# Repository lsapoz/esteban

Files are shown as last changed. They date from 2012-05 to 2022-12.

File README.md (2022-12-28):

# Northwestern Design Competition 2012

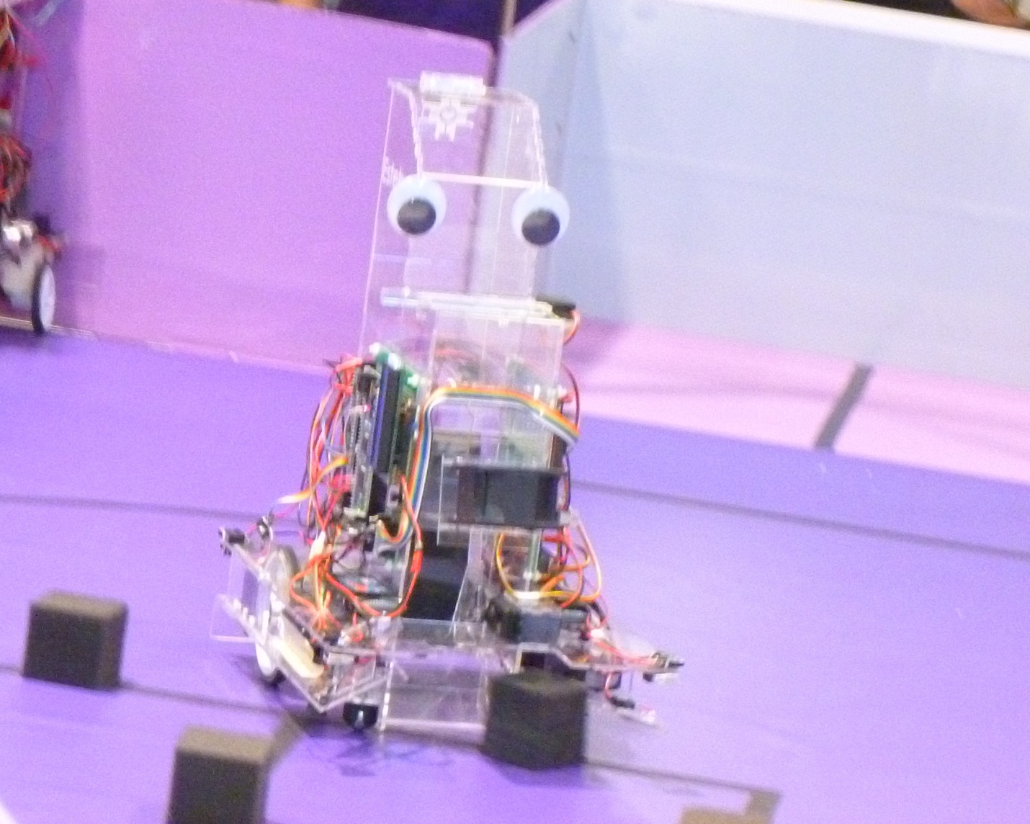
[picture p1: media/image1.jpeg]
Esteban


## Overview

I was cleaning up my dropbox and stumbled upon all the files for Esteban, the robot Michael Chen and I built for the 2012 Northwestern Autonomous Robot Design Competetion. I thought github would be a better place to host the files, so here we are.

Since all the code was stored as snapshots (i.e. the [Final.doc](https://phdcomics.com/comics.php?f=1531) approach to version control), I turned each snapshot into a distinct commit and spoofed the dates using [git-redate](https://github.com/PotatoLabs/git-redate). 

## Related Links
- [El Viaje de Esteban](https://viajedeesteban.tumblr.com/) - a project blog chronicling the build
- [Match Video](https://www.youtube.com/watch?v=B897-lxEE_c)
- [Competition Rules](https://sites.google.com/site/dcnuinfo/previous-competition-rules/2012-competition-rules)
- [Mechatronics Lab Wiki](http://hades.mech.northwestern.edu/index.php/Northwestern_Design_Competition#DC2012)
- [Article](https://www.mccormick.northwestern.edu/news/articles/2012/05/2012-design-competition-winners.html)

## The Team

The team consisted of myself, a mechanical engineering junior, and
Michael Chen, a civil engineering junior. This was our second design
competition.

All aspects of the design were done together. This covers the initial
brainstorming of ideas, building mockups to see what worked and what
didn't, and all major mechanical, electrical, and software design
decisions. For example, deciding the dimensions of a part, discussing
what kind of circuit would accomplish a task best, and what sort of
approach an algorithm would take to tackle a problem were all at the
very least discussed. As a result, both of us have an intimate knowledge
of every aspect of the robot.

In actually building the robot, tasks were often split up to maximize
efficiency. However, we would often work on parts in tandem so that we
could still talk to each other about what we were doing. So while we
designed the chassis together, I was the one who actually created all of
the CAD files and used them to cut out the chassis on the laser cutter.
I also wrote all of the code that the robot ran on. However, Mike would
go in and tune different parts of the code that needed tuning. Mike also
implemented most of the electrical design.

The product of our work was the robot named Esteban. He bore two giant
googly eyes which served as the namesake for our team: "Googly Eyes."

## Strategy

A quick run-down of the competition revealed three key points that would
end up influencing our design above all others

-   The cubes were made out of a light foam which could not be detected
    easily from afar with simple sensors

-   Three times as many points were scored for cubes deposited in the
    bonus zone rather than the regular scoring zone

-   There are massive penalties for manipulating more than five cubes at
    a time

Early on we resigned ourselves to trying to find cubes using some sort
of efficient random algorithm rather than actually detect them. This was
based on the assumption that cubes would be moved around a lot during
the competition. Later on we realized that actually programming in
several possible hard coded paths was a more reliable option. We would
program paths meant to drive over the starting positions of 8 or so
cubes. However, after four cubes were actually picked up we would exit
the path and drive towards the scoring zone to deposit them.

Encoders were used for keeping track of Esteban's location. Because of
collisions and the moving scoring zone, we needed to reset our location
often. Resetting on the long axis was accomplished by driving over the
center line. Resetting after exiting the scoring zone was done by
hitting one of the side walls to reset angle, and then using either the
center line or a cube to reset overall position.

We couldn't detect cubes from afar, but a series of break beams were
used to determine when they entered our chassis. We took advantage of
the cube's light material by using two fans: one to blow them into a
tower and one to blow them out.

A laser attached to a servo was used to find the scoring zone, which was
covered in retroreflective tape. Esteban turns himself so that his back
is facing the scoring zone and then drives towards the center line, 6
feet away from the zone. The laser is then swept, and the "average"
angle of the laser for which the beam bounces back is found. Esteban
then turns this average angle and begins to drive towards the zone. The
same technique is repeated three feet from the zone and one and a half
feet from the zone. This helps adjust for the movement of the zone.

## Mechanical Design

### Parts list

-   3 acrylic sheets -- 0.118"x12"x24"

-   1 1.5" acrylic hinge

-   1 4" long 3/8" diameter acrylic rod

-   2 90mm wheels

-   2 4mm universal mounting hubs

-   2 ¾" metal ball casters

-   2 drive motors

-   2 small servos

-   1 large servo

-   1 laser

-   7 bright red LEDs

-   8 phototransistors

-   8 push buttons

-   2 capacitive encoders

-   1 60mm case fan

-   1 80mm case fan

-   4 7.4 V polymer lithium ion batteries

-   1 11.1 V polymer lithium ion battery

-   A pair of 40mm googly eyes

### Chassis CAD Drawing

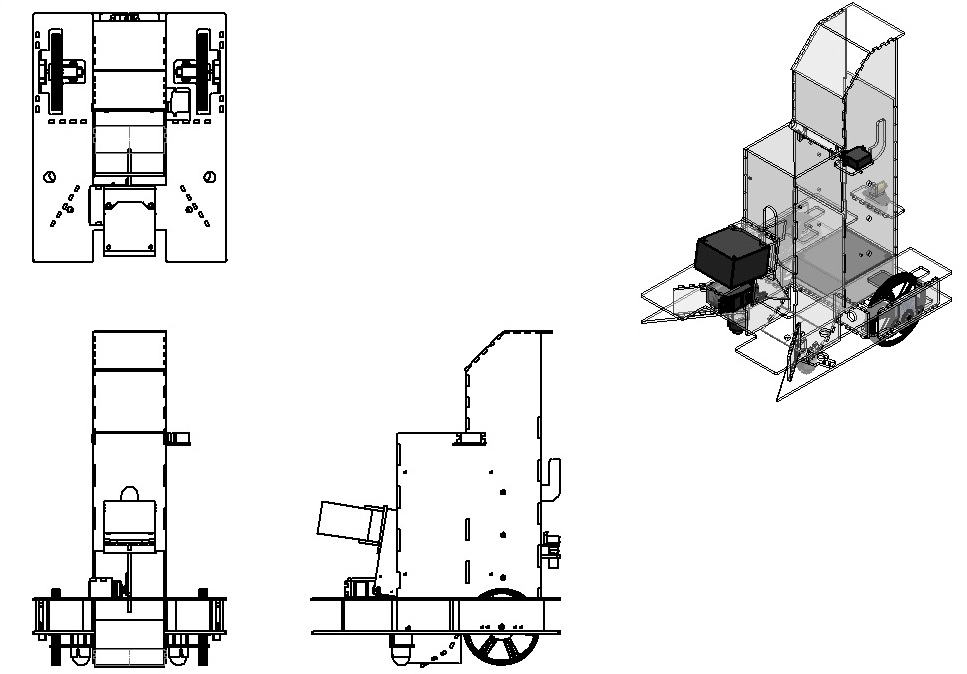
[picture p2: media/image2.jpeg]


### CAD -- Sheets for Laser Cutting

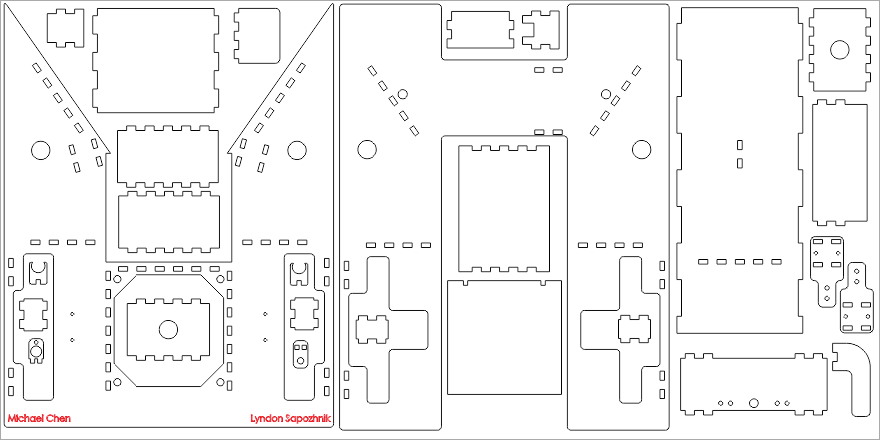
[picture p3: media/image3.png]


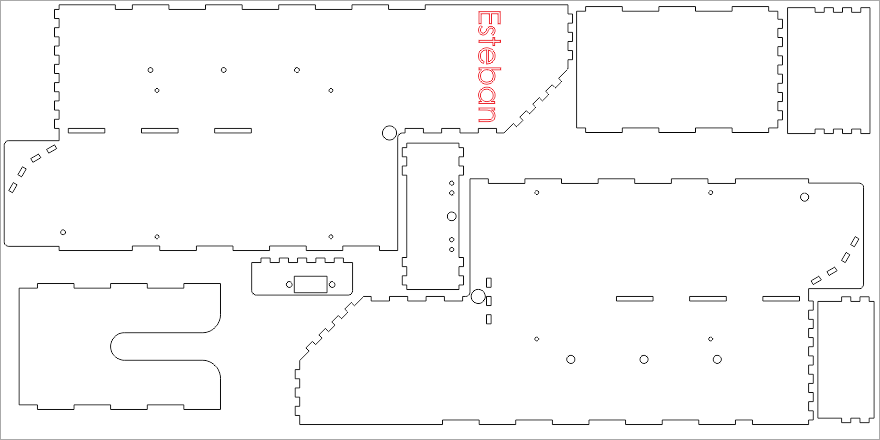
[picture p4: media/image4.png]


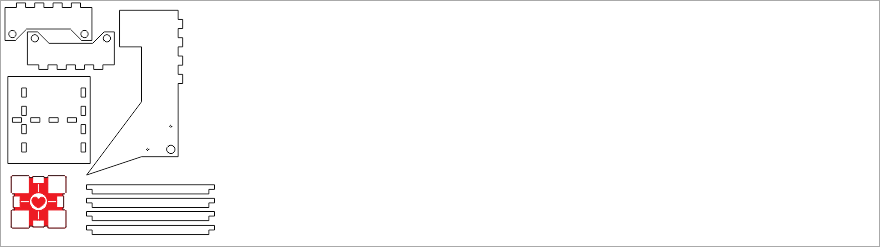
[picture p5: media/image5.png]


### Locomotion Technique

The two drive motors provided to us were used to move Esteban. They were
placed towards the back. Two metal ball casters were placed near the
front for balance.

PID motion control based on encoder feedback was implemented to control
the motors. The hope was that this would allow us to set a speed that
both motors would adhere to with little error, allowing for Esteban to
drive in straight lines and turn accurately. Unfortunately, a number of
things prevented this from working well in practice. One was that the
wheels would actually lift off the ground while driving. This was fixed
by placing steel bars by the wheels to weight them down and keep them on
the ground. Another was the poor relationship between voltage and speed;
setting a constant voltage would result in a widely varied speed. This
meant that even when controlling for the voltage using motion control,
the resulting speed would still vary so much that Esteban ended up
veering left or right while driving.

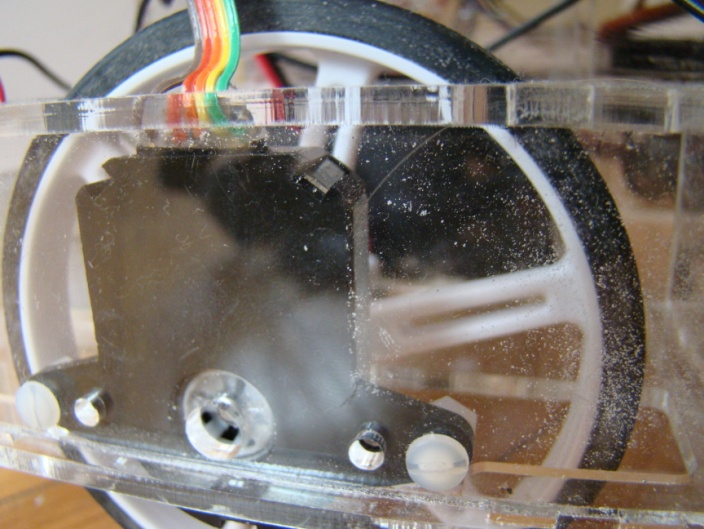
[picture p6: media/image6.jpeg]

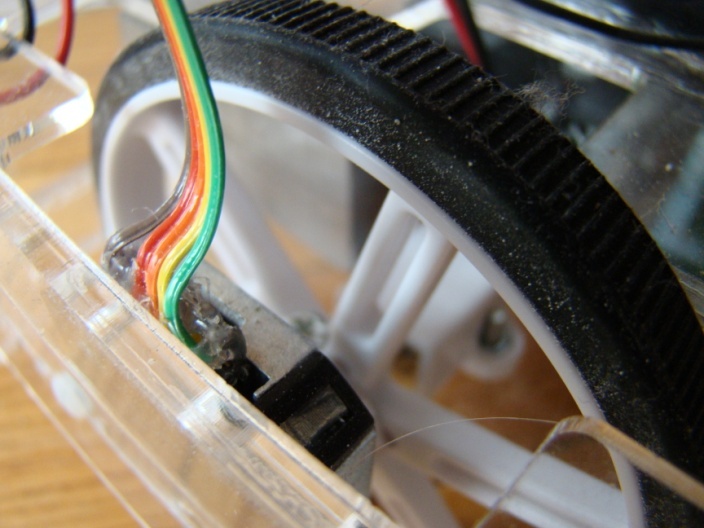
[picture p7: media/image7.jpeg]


Eight push buttons were used for collision detection; two at each
corner. The two at each corner are tied together so we only had
information about which corner was colliding with something.

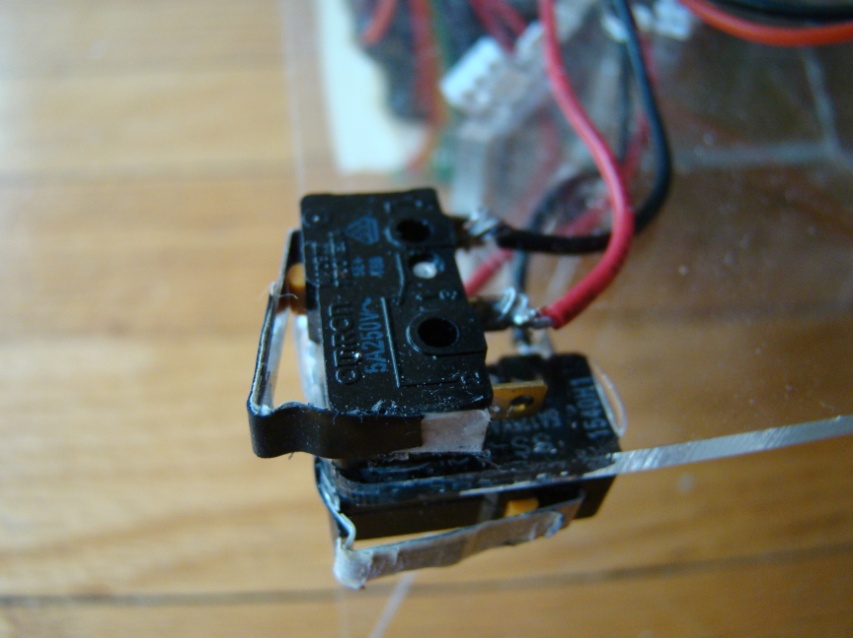
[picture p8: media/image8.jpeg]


### Interaction with the cube

The front of Esteban is shaped like the letter "V," wide at the front
and narrowing down to a channel slightly wider than the cubes. Once a
crate is detected, a 60mm case fan is lowered using an acrylic arm and
turned on. This blows the cube up onto a ramp and into Esteban's tower.

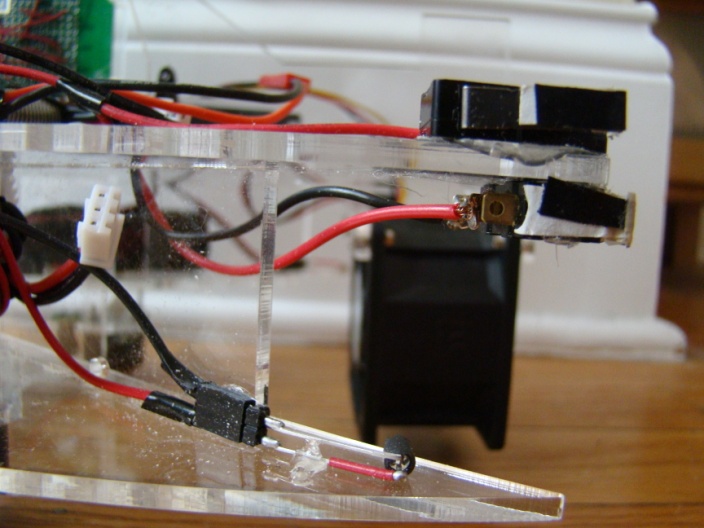
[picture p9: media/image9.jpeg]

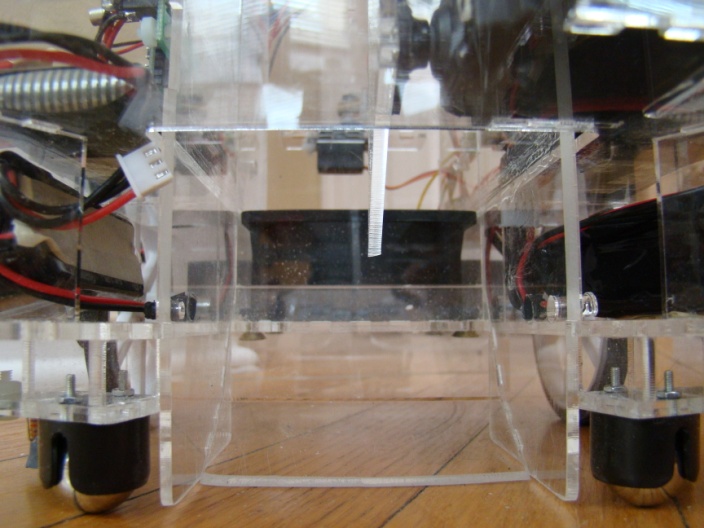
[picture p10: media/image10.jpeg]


Entrance into the tower was controlled by a door attached to a servo.
The door was opened to let cubes in and closed to keep them in. Once
Esteban was in the scoring zone, he would drive to the back wall and
turn on the tower fan, which would blow all the cubes out.

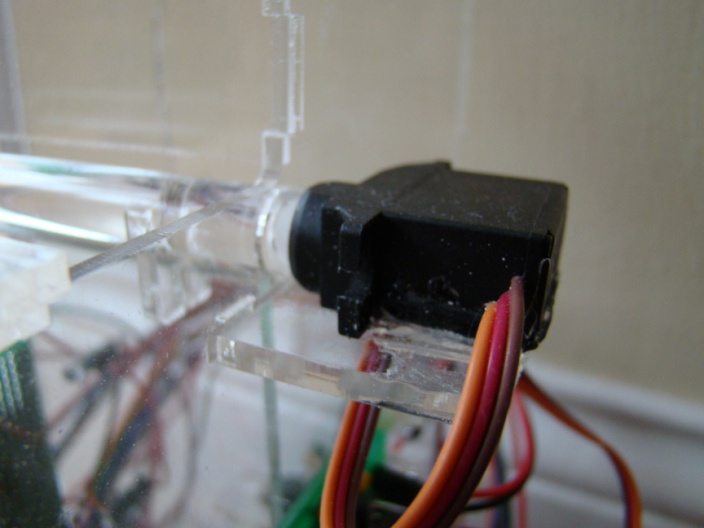
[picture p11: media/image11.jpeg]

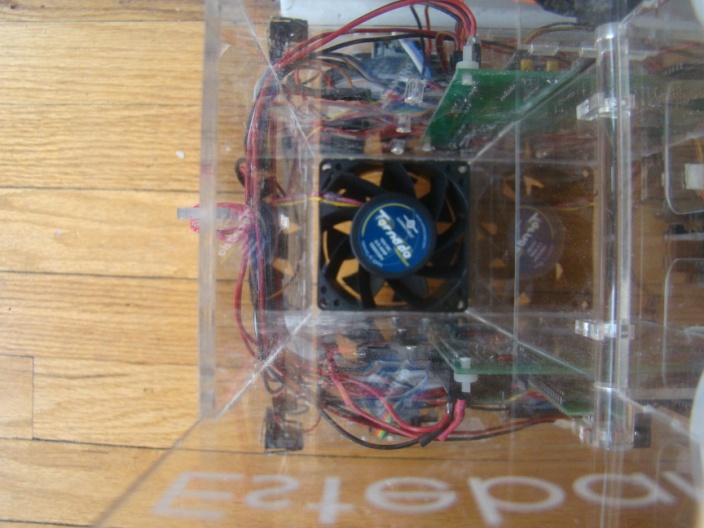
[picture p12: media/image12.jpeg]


To keep the cubes from shooting out too far and missing the bonus zone,
a "doggy door" was attached to the exit using an acrylic hinge. This
alters the cubes trajectory so they point downwards more than straight
out.

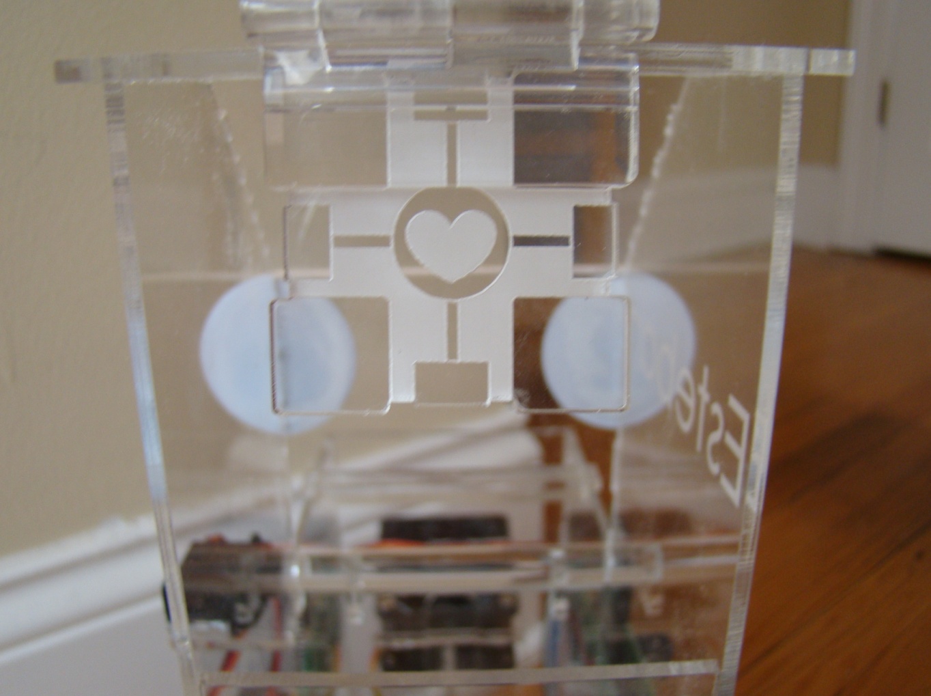
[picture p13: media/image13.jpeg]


The tower was capable of holding up to three cubes. The fourth cube was
stored just outside the tower. The front fan would be turned on but the
tower door would be kept closed, causing the cube to be shot up until it
hit a thin acrylic barrier. The front fan would then be turned off and
rotated back into its resting position. Thanks to the fan arm's unique
shape, it actually holds the fourth cube in place. We can then blow it
into the tower at a later point.

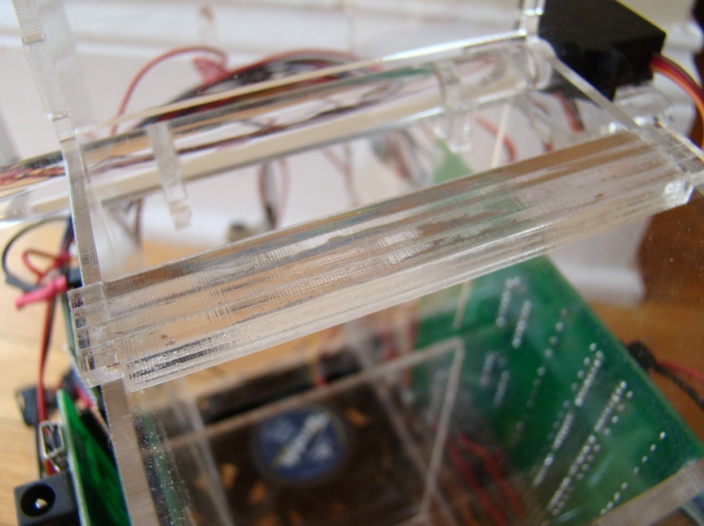
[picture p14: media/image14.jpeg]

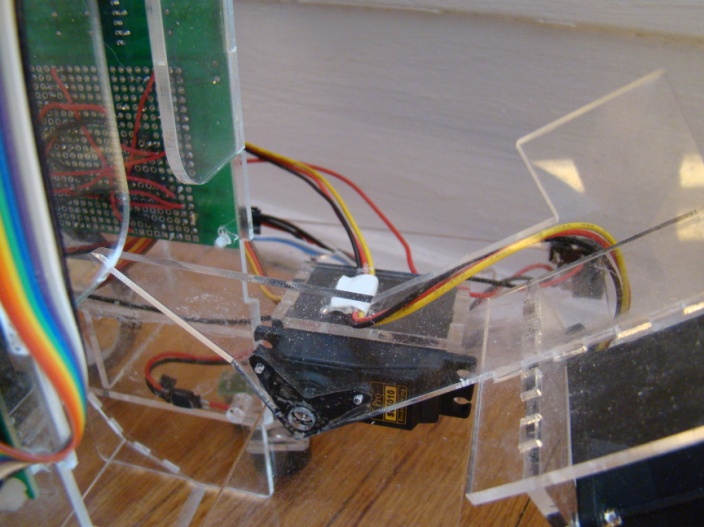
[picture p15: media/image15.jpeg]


## Electrical Design

### Actuator Controllers

One large servo was used to control the fan arm. One small servo was
used to control the tower door, and another was used to control the
laser.

### Sensors

Five breakbeam sensors were used for detecting cubes inside Esteban: one
at the very front of the chassis, one just in front of the channel (near
the middle of the chassis), and three in the tower. The breakbeam
sensors were simply a bright LED pointing at a phototransistor. To
control for ambient light, we would read the phototransistor twice in a
cycle: once with the LED on and once with it off. We would use the
difference between the two readings as our check; if it dipped to 0, we
knew a cube was there.

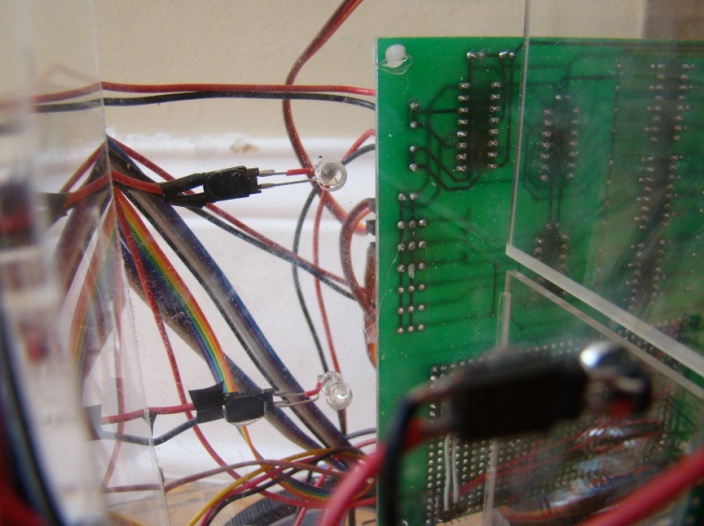
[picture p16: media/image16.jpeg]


Two color sensors were used for determining the current color of the
board. They were simply an LED and phototransistor placed next to each
other, pointed at the ground. White reflected a lot, purple
significantly less, and black almost not at all. The two color sensors
were "pulsed" just as the breakbeams were to control for ambient light.
Heat shrink was used as an additional precaution.

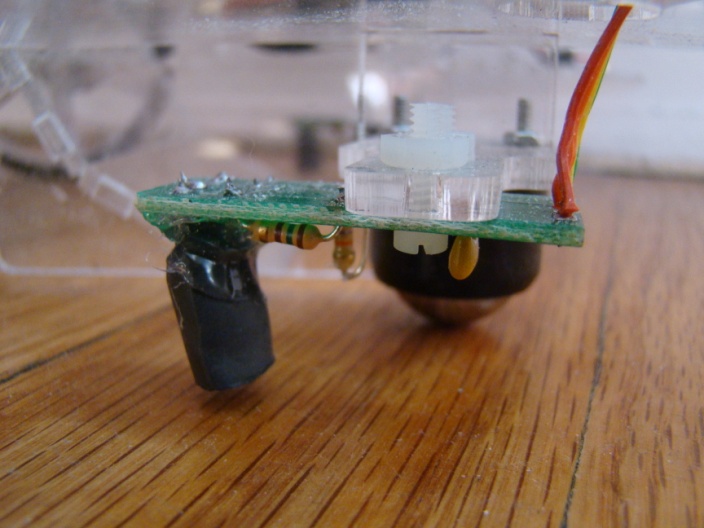
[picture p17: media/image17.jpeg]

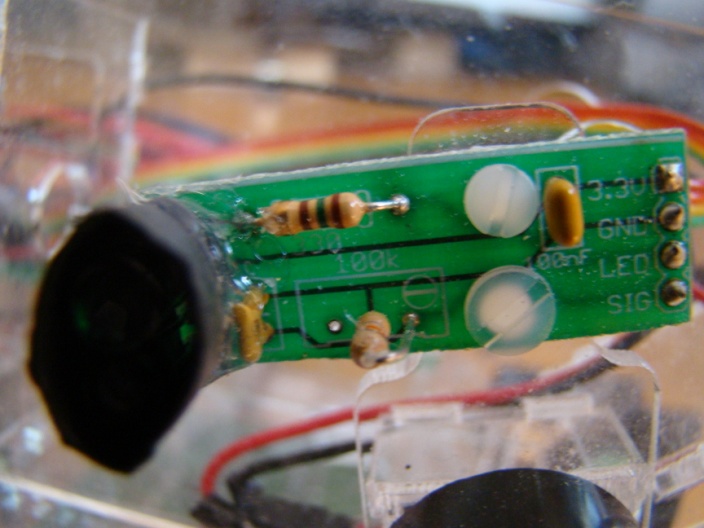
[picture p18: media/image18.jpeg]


A laser/phototransistor combo attached to a servo was used for finding
the scoring zone. It was blinked on and off in the same way the LEDs
were to control for ambient light.

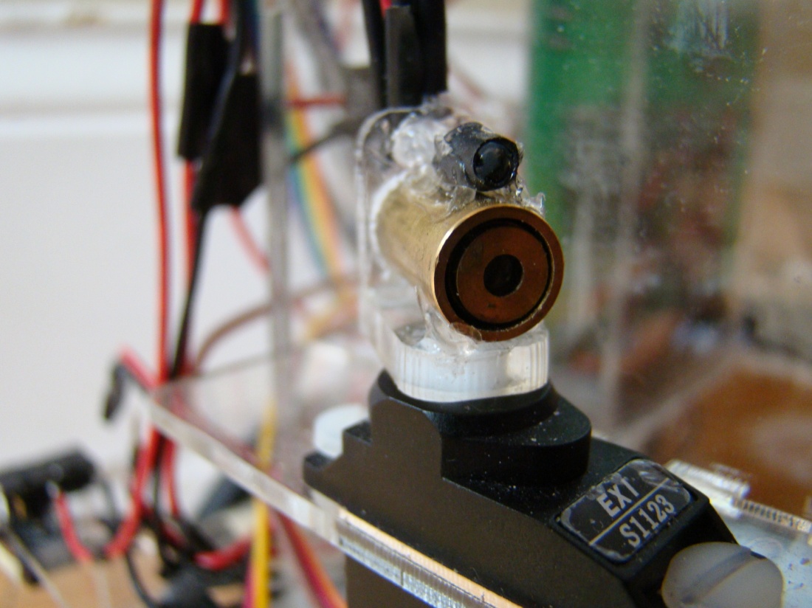
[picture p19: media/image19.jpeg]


The encoders used for motion control and location awareness were each
fed into their own dsPIC33. These were then connected to the main PIC32
using SPI communication.

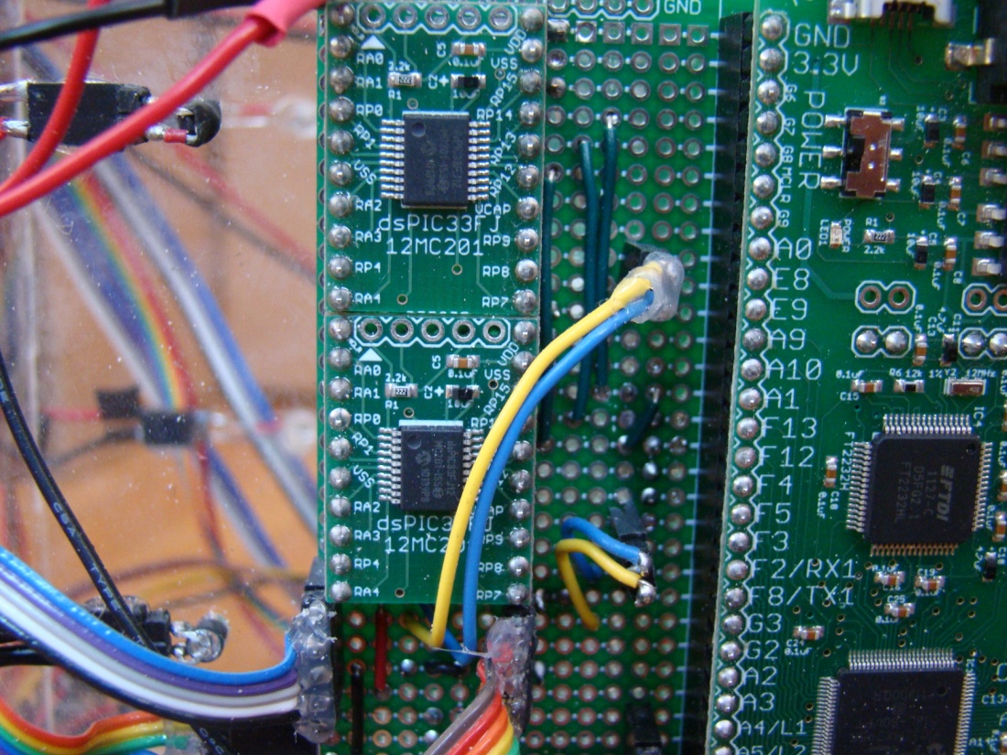
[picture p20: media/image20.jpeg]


All the sensors were connected to the PIC32 in the following way:

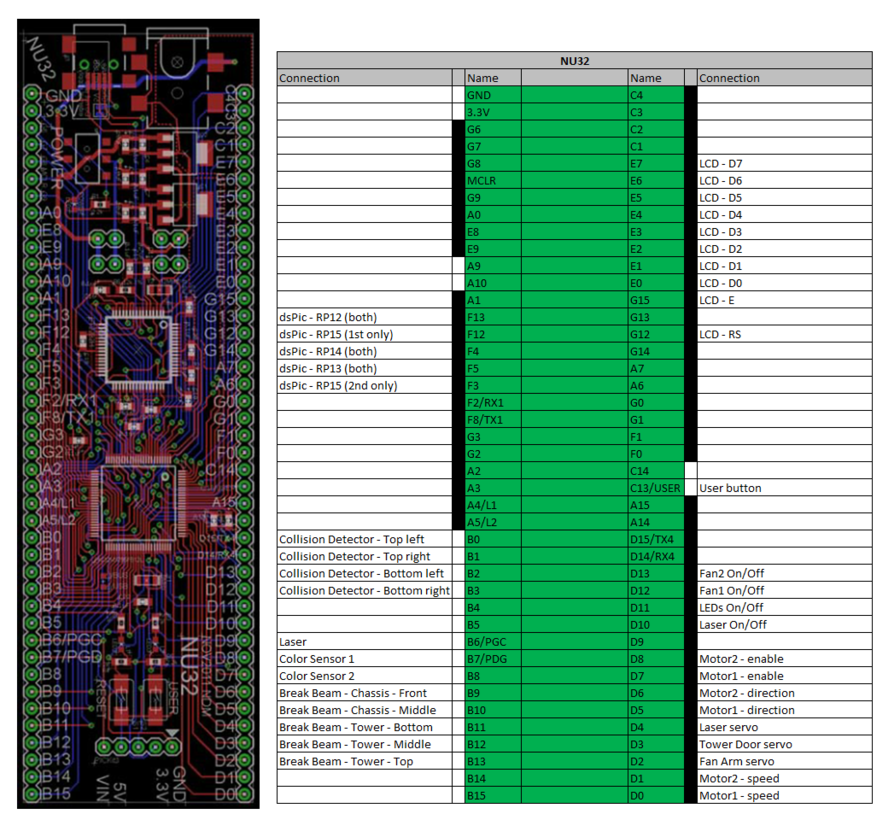
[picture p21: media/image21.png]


### Power Management

Rechargeable polymer-lithium ion batteries were used this year. All were
connected to voltage regulators so that the same voltage would be always
supplied to our components. One 7.4 V battery was used to power the
PIC32, one to power the logic, and two in series to power the fans. One
11.1V battery was used to power the motors.

### Breakout Boards

The two breakout boards were mounted to Esteban's sides.

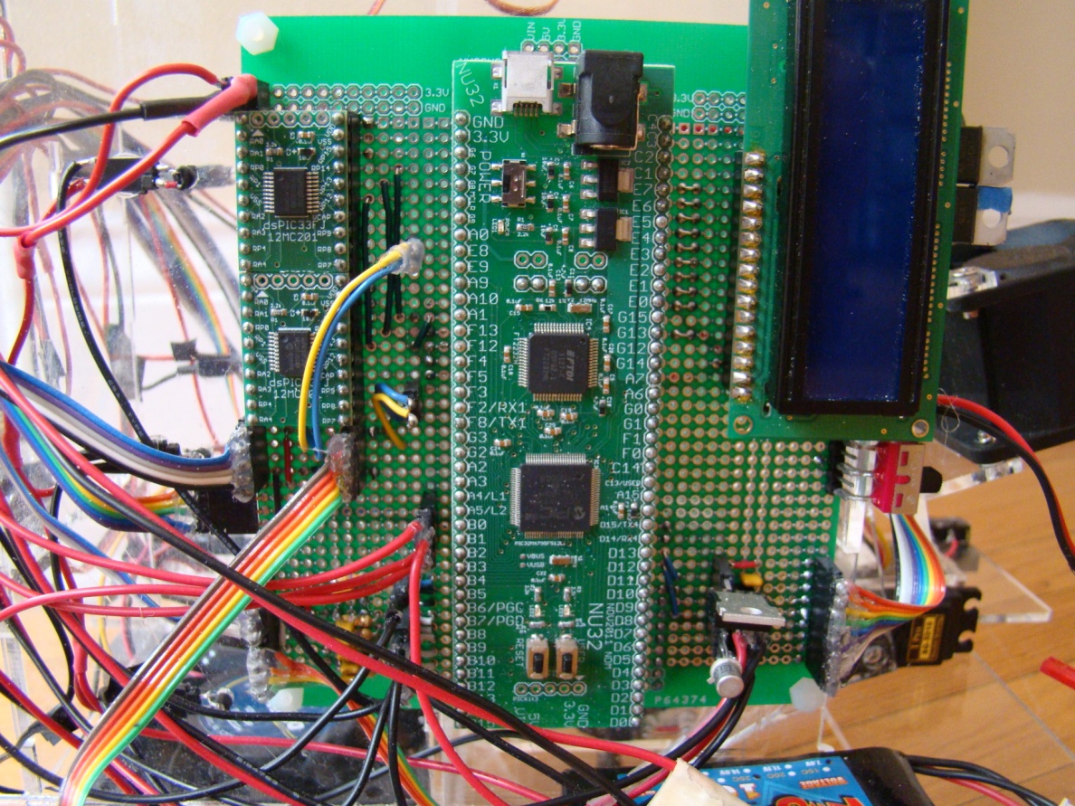
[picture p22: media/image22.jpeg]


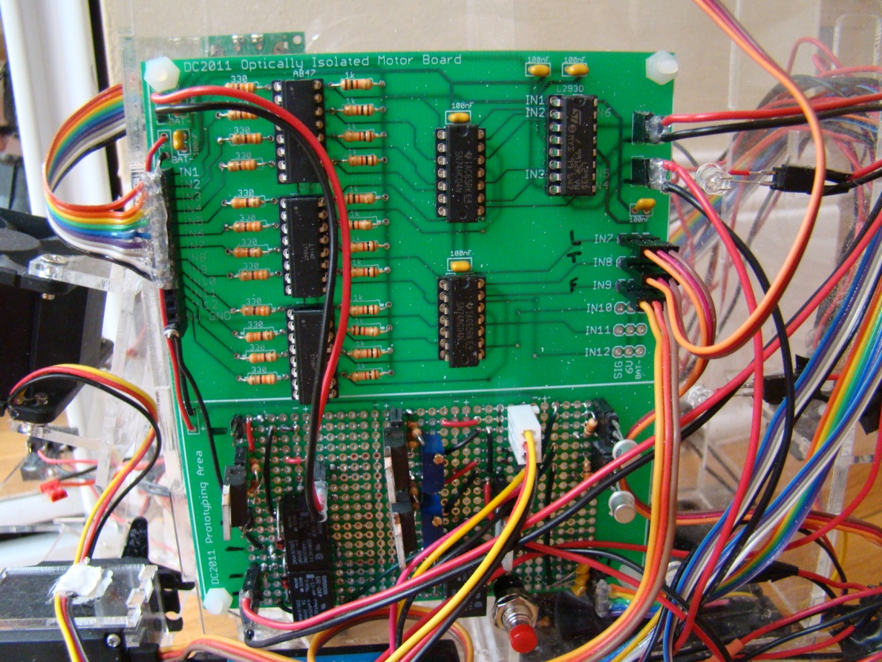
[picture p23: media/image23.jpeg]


## Programming

The program was split across four user written files + four provided
(NU32.h and .c, LCD.h and .c).

They were:
```c
- main.h     // initialization and interrupts
- data.h     // definition of constants, conversion formulas, and global variables
- library.h  // declaration of all functions
- library.c  // initialization of all functions
```

### Functions
```c
// Timer functions

void initCoreTimer(void); // initialize the core timer to interrupt every 1 ms

void initTimer4Interrupt(void); // turn on timer4 interrupt at 250 Hz

void initTimer5Interrupt(void); // turn on timer5 interrupt at 10 Hz

// Pin Initialization functions

void initChangeNotification(void); // enable pull up resistors for collision detection pins

void initDigitalOut(void); // enable all digital outs

void initAnalogInput(void); // read in all used analog in pins

void initOutputCompare(void); // turn on both motors and all three servos

// Encoder functions

void initEncoderSPI(void); // initialize SPI communication with the dsPICs at 8MHz

long getEncoder1(int reset); // get the current number of ticks of encoder1

long getEncoder2(int reset); // get the current number of ticks of encoder2

// Servo functions

void rotateFanArm(int servoPos); // rotate the fan arm to a desired position

void rotateTowerDoor(int servoPos); // rotate the tower door to a desired position

int sweepLaser(float feet); // sweep the laser and calculate the distance to the zone

// Fan functions

void blowCubeIn(); // blow a cube into the tower

void blowCubeUp(); // blow a fourth cube up outside of the tower for storage

void blowCubesOut(); // blow all cubes in the tower out

void blowCubeInAndOut(); // blow the fourth stored cube into the tower and straight out

void checkForCubes(); // while driving, stop if a cube is detected so it can be captured

// Driving Functions

void setMotorSpeed(int dutyCycle1, int dutyCycle2); // set the voltage for both motors

void reverseDirection(); // change the voltage appropriate to drive in reverse

void driveDistance(float inches, int mode); // drive forwards or backwards a certain distance

void turnAngle(int degrees); // turn a certain amount of degrees

void driveToCenter(); // drive until the center line (i.e. ground color changes)

void driveToZone(); // drive to center, sweep laser multiple times on the way to the scoring zone

void resetAngle(); // keep colliding and adjusting angle until perpendicular

void resetAngleOnWall(int wall); // collide with the wall until perpendicular

void resetAngleInZone(); // collide with the back wall until perpendicular

void exitAndResetOnRight(); // exit the scoring zone and reset angle on the right wall

void exitAndResetOnLeft(); // exit the scoring zone and reset angle on the left wall

// Sweep Patterns

void firstSweepPattern1(); // first cube in front, two on middle line, one on first line

void firstSweepPattern2(); // first cube in front, three on second line

void firstSweepPattern3(); // the four cubes on the diagonal from the starting position

void firstSweepPattern4(); // reset angle on wall at center line, then all on middle line

void firstSweepPattern5(); // the four closest cubes

void secondSweepPattern1(); // three on middle line, two on fourth line

void secondSweepPattern2(); // first cube upon resetting on right wall

void secondSweepPattern3(); // three on diagonal leading from the cube in secondSweepPattern2();

void randomSweepPattern(); // drive completely randomly

void wallToWallSweepPattern(); // sweep the entire field, wall to wall

// Stringing it all together

void firstSweep(); // firstSweepPattern4()+exitAndResetOnRight()

void secondSweep(); //secondSweepPattern2()+3()+ exitAndResetOnLeft()

void randomSweep(); // drive randomly searching for cubes
```
### main

#### main
```
{
    Call every initialization function
    while (1) {
        if (user button is pressed) {
            firstSweep();
            secondSweep();
        }
    }
}
```

#### Core Timer Interrupt (1000 Hz)
```
{
    increment the global time variable
}
```

#### Motion Control Interrupt (250 Hz)
```
{
    Read in encoder1 and encoder2 and perform PID control based on the driving state (driving straight or turning)
}
```

#### Sensor Interrupt (10 Hz)
```
{
    Turn on all the LEDs
    Read all the phototransistors
    Turn off all the LEDs
    Read all the phototransistors
    Calculate the difference between the ON and OFF values
    Determine the number of crates in the machine
    Determine the color being read by the color sensors
    Determine if any collision detectors are being tripped
}
```

## Results

### Midterm Milestone

For the midterm milestone, we had cut and assembled the first version of
Esteban. While testing with him we found that cubes would often get
stuck inside Esteban because they very easily rotate; we had to design
for 2 √3, not 2 √2. In order to make sure the cubes could traverse
Esteban's interior once we expanded relevant dimensions, we rather
recklessly tore him apart and taped him back together. Once we were
satisfied we began altering the design. In the meantime, "Frankenbot"
was used to clear the Midterm Milestone.

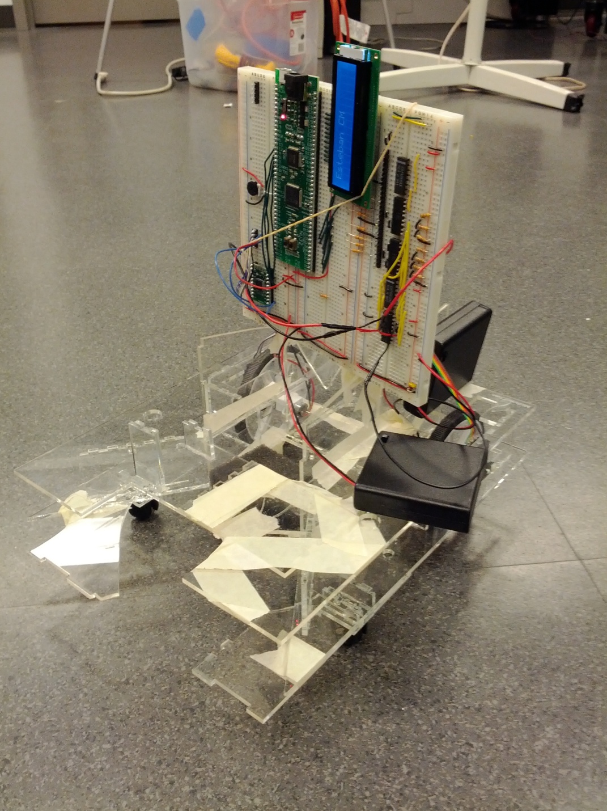
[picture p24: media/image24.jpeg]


### Pre-Competition Demonstration

Every single system but driving was up and running great for the
pre-competition demonstration. We still had issues getting the robot to
drive in a straight line reliably, but Esteban was at least turning
fairly accurately. What remained for the final week was fixing this
issue to the best of our ability, and actually coding in strategy.

### Competition Results

Getting the robot to drive straight accurately was an exercise in
frustration. We began to throw in a whole host of precisely tuned
constants into the PID motion control code, making something that was
once simple into something horrendously complex. Additionally, these
constants had to be retuned as our motors degraded. In the 24 hours
leading up to the competition, both of our motors ended up losing the
ability to drive backwards and had to be replaced. After these accidents
we decided to only tune what we thought were our two best paths for the
competition. We decided that consistency would probably pay off in the
competition more than diversity.

The decision ended up paying off, as we were seeded first and we won
first place. Esteban successfully executed his two paths each time.
Occasionally we would drift too left or right to pick up a cube we had
intended to pick up. One time a cube overshot the bonus zone and fell
out of the arena. But we always ended our rounds with at least six cubes
in the bonus zone. That was enough to carry us to victory.

## Takeaways

Thanks to the lessons learned from competing in last year's design
competition, we understood what needed to be done this year to build a
great robot. Esteban was very precisely engineered, and it shows. He
executed everything we meant for him to do exactly as we meant for him
to do it, with the exception for driving.

We meant to use some sort of feedback control for driving this year, and
our choice of PID simply did not cut it. Perhaps we would have gotten
better performance had we based the motion control on current control
rather than just encoder feedback. If there had been time, I would have
definitely explored more avenues of getting reliable driving.

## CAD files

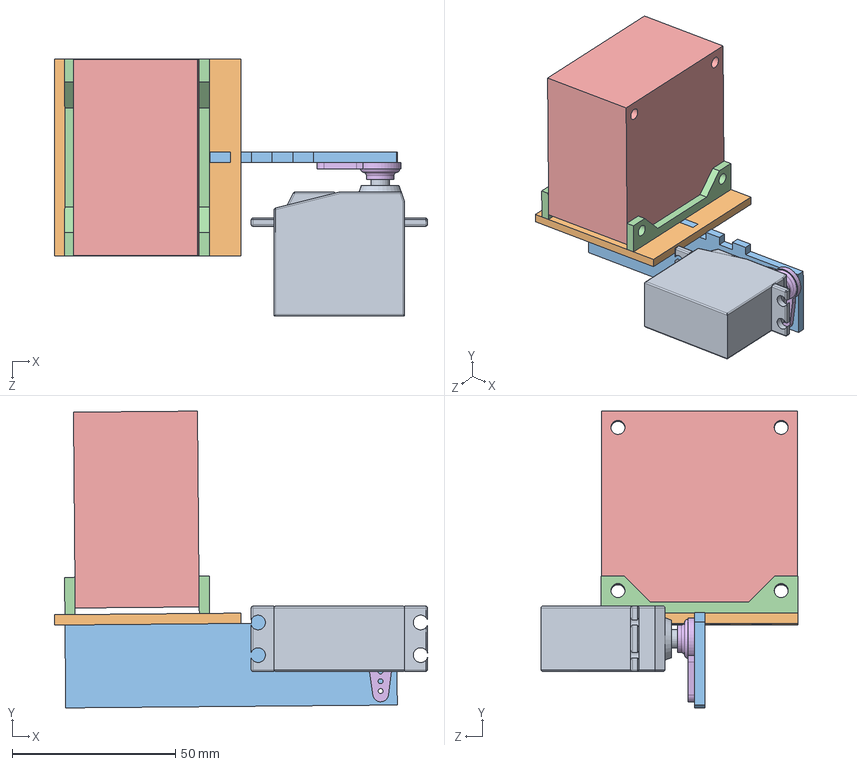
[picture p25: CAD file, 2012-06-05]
model/fan_arm.SLDASM
114.3 x 90.9 x 78.8 mm
servo_large
fan_arm_horizontal
fan_arm_vertical
fan_arm_holder x 2
fan_60mm
servo_handle_two

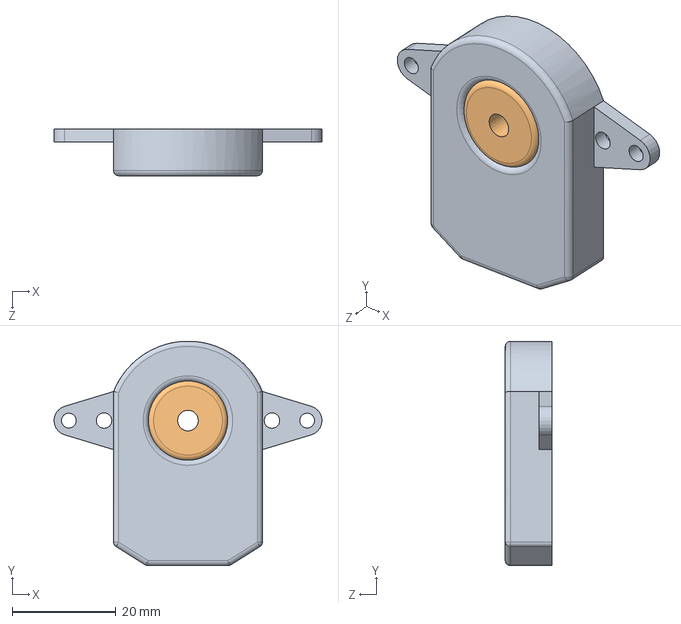
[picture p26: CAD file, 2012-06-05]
model/encoder.SLDASM
51.8 x 43.4 x 9.00 mm
encoder_base
encoder_sleeve

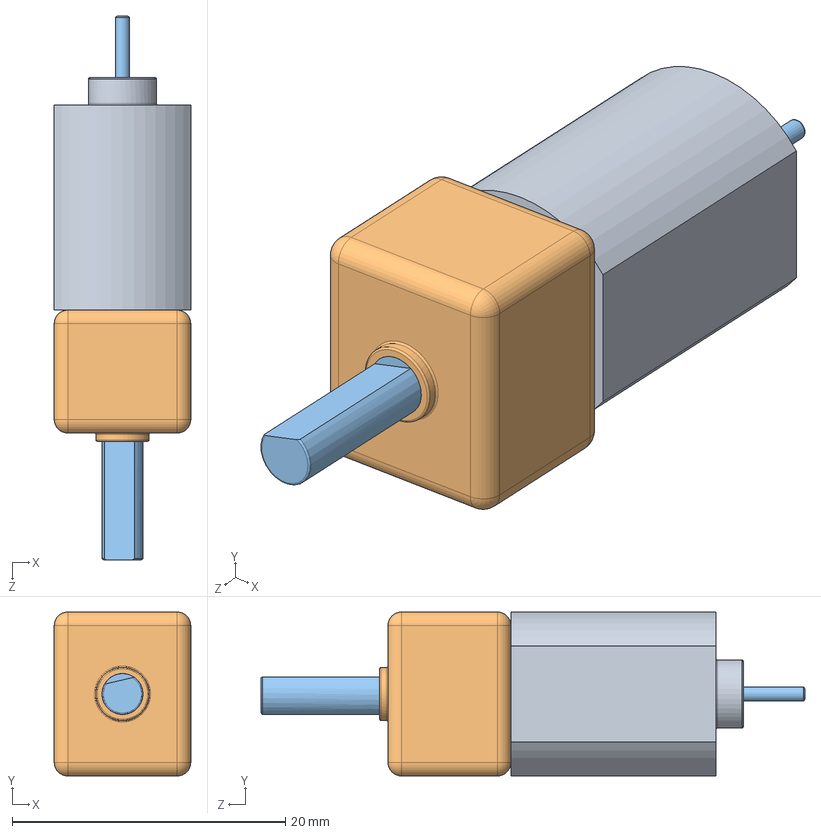
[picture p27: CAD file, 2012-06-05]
model/motor.SLDASM
10.0 x 12.0 x 39.8 mm
motor_casing
motor_gearbox
motor_shaft

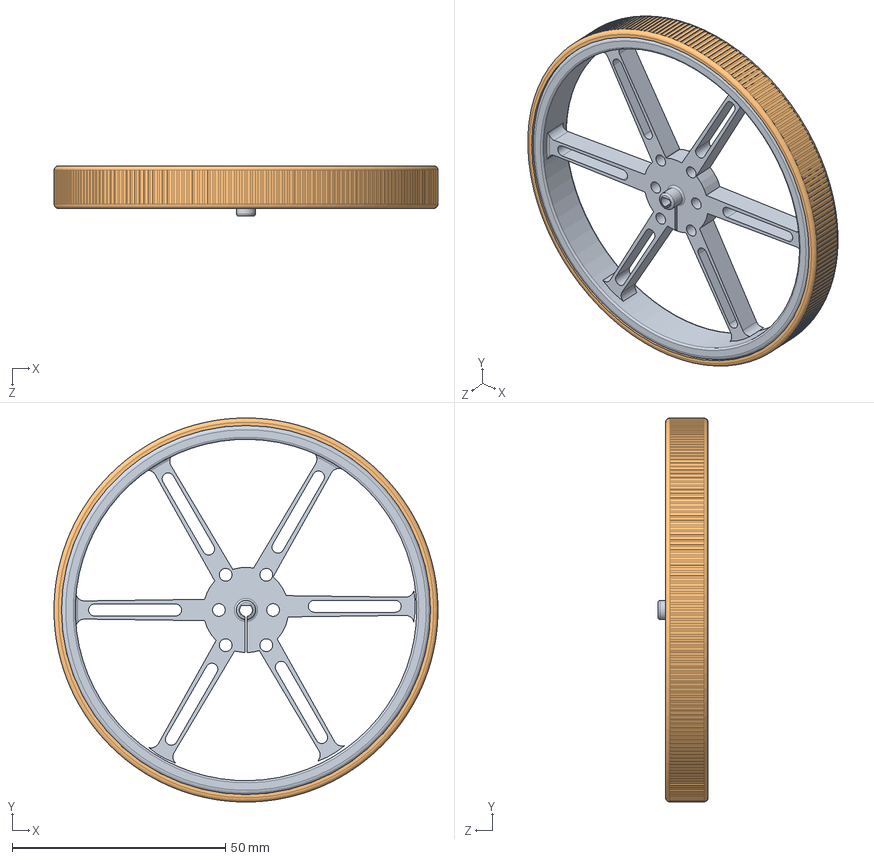
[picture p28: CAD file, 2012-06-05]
model/wheel_90mm.SLDASM
90.0 x 90.0 x 11.8 mm
wheel_base_90mm
wheel_tire_90mm

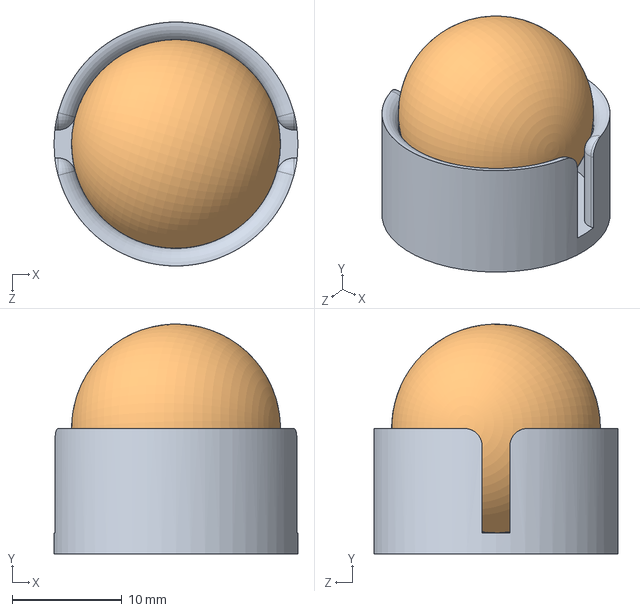
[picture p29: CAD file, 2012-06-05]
model/caster.SLDASM
22.3 x 20.9 x 22.3 mm
caster_holder
caster_wheel

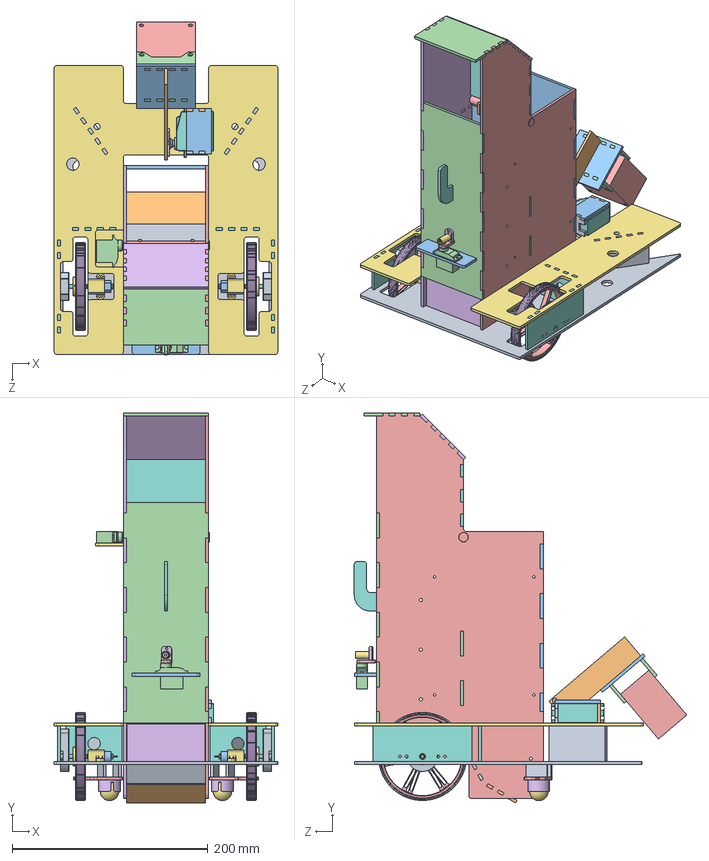
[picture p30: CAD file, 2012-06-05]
model/esteban.SLDASM
228.6 x 398.8 x 340.1 mm
chassis_base
motor_gearbox x 2
motor_casing x 2
motor_shaft x 2
chassis_fan_sidepanel
chassis_fan_sidepanel_servo_side
motor_bracket x 2
chassis_encoder_support x 2
chassis_layer_bridge x 2
door_rod_holder x 2
door
chassis_fan_frontpanel
caster_spacer x 2
caster_holder x 2
caster_wheel x 2
servo_large
servo_handle_two
fan_arm_vertical
fan_arm_horizontal
fan_arm_holder x 2
wheel_base_90mm x 2
wheel_tire_90mm x 2
universal_mounting_hub x 2
dowel_4mm x 2
encoder_base x 2
encoder_sleeve x 2
laser_servo_holder
servo_small x 2
fan_60mm
fan_80mm
chassis_layer_2
chassis_layer_bridge_middle x 2
servo_holder_with_hole
servo_holder
servo_holder_roof
chassis_backpanel
door_rod
chassis_fan_roof_angle
door_servo_holder
wire_hook
chassis_arc_top
chassis_arc_bottom
chassis_really_front_panel
chassis_fan_roof_flat
laser_holder_holder
laser_holder
laser
chassis_top_frontpanel
caster_bridge x 4

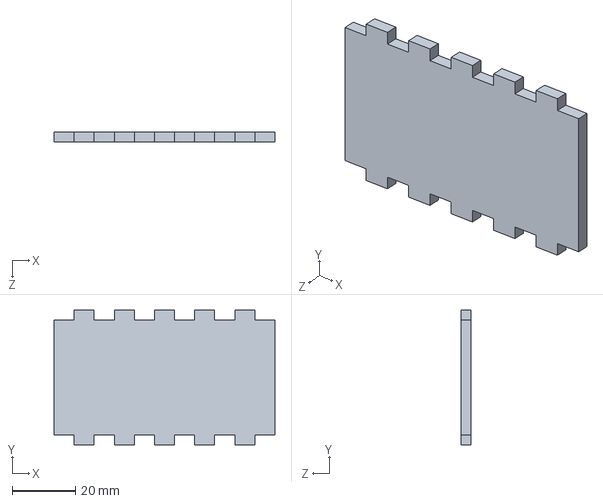
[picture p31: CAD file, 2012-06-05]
model/chassis_layer_bridge.SLDPRT
69.8 x 42.5 x 3.17 mm

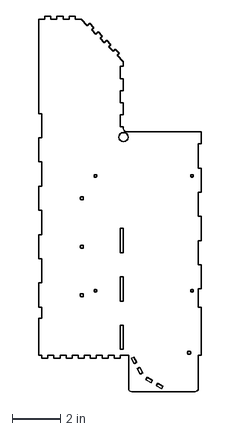
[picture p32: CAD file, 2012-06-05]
model/Laser Cutter/chassis_fan_sidepanel.DXF
6.71 x 15.5 in

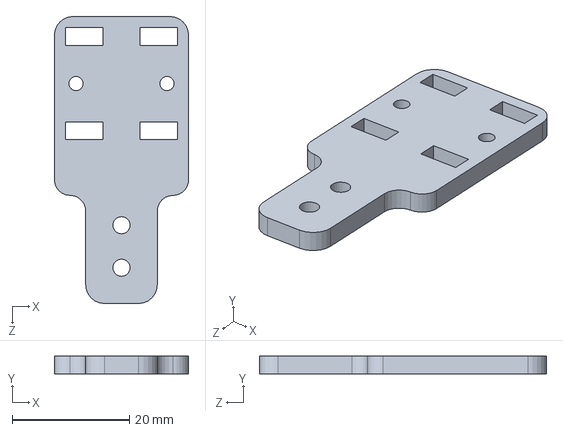
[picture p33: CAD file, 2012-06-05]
model/caster_spacer.SLDPRT
22.9 x 3.00 x 48.9 mm

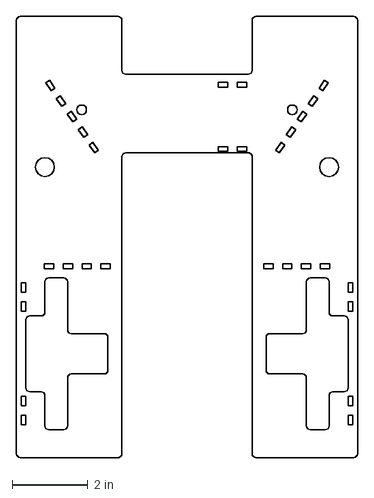
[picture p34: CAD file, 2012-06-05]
model/Laser Cutter/chassis_layer_2.DXF
9.00 x 11.6 in

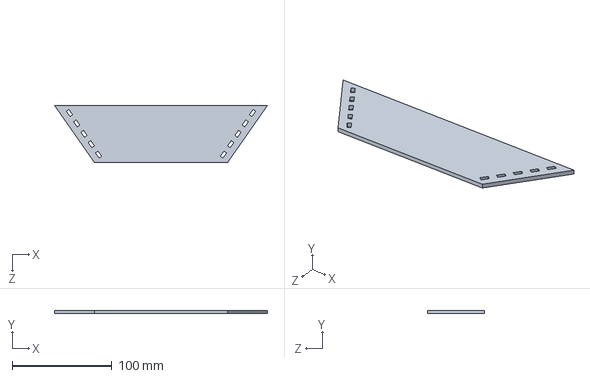
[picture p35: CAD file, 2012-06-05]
model/chassis_fan_arm_layer.SLDPRT
213.1 x 3.17 x 57.1 mm

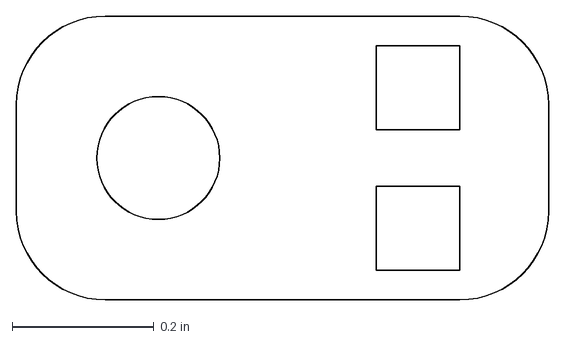
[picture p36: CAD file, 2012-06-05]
model/Laser Cutter/laser_holder_holder.DXF
0.75 x 0.4 in

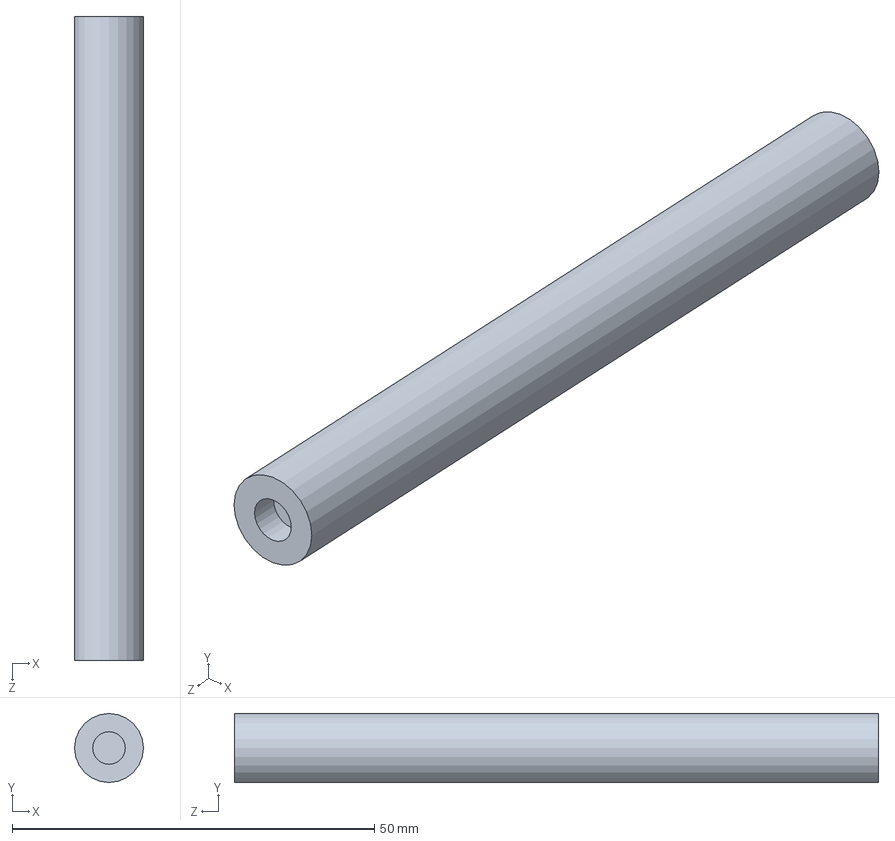
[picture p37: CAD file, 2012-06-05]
model/door_rod.SLDPRT
9.53 x 9.53 x 88.9 mm

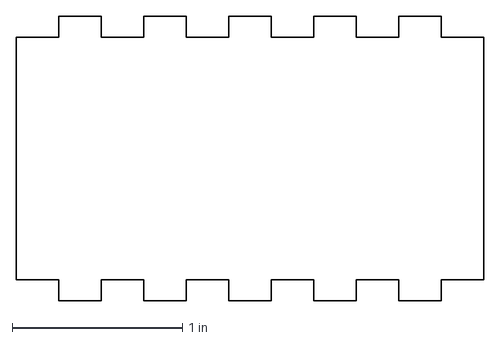
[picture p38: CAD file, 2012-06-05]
model/Laser Cutter/chassis_layer_bridge.DXF
2.75 x 1.68 in

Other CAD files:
model/Laser Cutter/chassis_fan_sidepanel_servo_side.DXF
model/wire_hook.SLDPRT
model/Laser Cutter/chassis_base.DXF
model/motor_shaft.SLDPRT
model/Laser Cutter/caster_bridge.DXF
model/Laser Cutter/caster_spacer.DXF
model/Laser Cutter/chassis_arc_bottom.DXF
model/Laser Cutter/chassis_arc_top.DXF
model/Laser Cutter/chassis_backpanel.DXF
model/Laser Cutter/chassis_encoder_support.DXF
model/Laser Cutter/chassis_fan_frontpanel.DXF
model/Laser Cutter/chassis_fan_roof_angle.DXF
model/Laser Cutter/chassis_fan_roof_flat.DXF
model/Laser Cutter/chassis_layer_bridge_middle.DXF
model/Laser Cutter/chassis_really_front_panel.DXF
model/Laser Cutter/chassis_top_frontpanel.DXF
model/Laser Cutter/door.DXF
model/Laser Cutter/door_rod_holder.DXF
model/Laser Cutter/door_servo_holder.DXF
model/Laser Cutter/fan_arm_vertical.DXF
model/Laser Cutter/laser_holder.DXF
model/Laser Cutter/laser_servo_holder.DXF
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

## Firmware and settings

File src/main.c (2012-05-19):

#include <plib.h>
#include "data.h"
#include "library.h"
#include "NU32.h"
#include "LCD.h"
#include "math.h"

//////MAIN
int main(void)
{
    // setup LED's and buttons
    NU32_Startup();

    // initalize global variables
    time = 0;
    goBack = 0;
    drivingState = STATIONARY;
    drivingMode = STATIONARY;
    numCrates = 0;
    crateInFront = 0;
    crateInMiddle = 0;
    terminalCounts1 = 0;
    terminalDegrees = 0;
    globalAngle = 0;
    cubesDeposited = 0;
    sweepRound = 1;

    collisionBottomLeft = 0;
    collisionBottomRight = 0;
    collisionTopLeft = 0;
    collisionTopRight = 0;

    // set temporary motion control variables
    Kp = 30;
    Kd = 120;
    Ki = 5;
    Kt = 12;
    K0 = 100;

    // init everything for the LCD
    setupLCD();
    LCDClear(0); // clear the LCD in case it still says something

    // initalize pins
    initChangeNotification();
    initDigitalOut();
    initAnalogInput();
    initOutputCompare();

    // initialize the SPI communication to the dsPIC
    initEncoderSPI();
    getEncoder1(TRUE);getEncoder1(TRUE); // call twice to set up function to account for rollover
    getEncoder2(TRUE);getEncoder2(TRUE);  // call twice to set up function to account for rollover
    
    // setup timers
    initCoreTimer();
    initTimer4Interrupt();
    initTimer5Interrupt();

    // print to the LCD
    sprintf(LCD_Out_Buffer,"Esteban 1");
    LCDWriteString(LCD_Out_Buffer, 1, 1);

    // initialize UARTS and interrupts
    NU32_EnableUART1Interrupt();
    NU32_Initialize();

    // print to the computer
    sprintf(NU32_RS232OutBuffer,"Esteban DC\r\n");
    NU32_WriteUART1(NU32_RS232OutBuffer);

    long blah = time;
    while(1) {
        char message[100];
//        if (!NU32USER) {
//            driveDistance(-12,PLAID);
//            while(drivingState != STATIONARY) {
//                float remaining;
//                if (collisionBottomLeft == 1) {
//                    remaining = terminalCounts1 - position1;
//                    terminalCounts1 = 0;
//                    turnAngle(-30);
//                    while(drivingState != STATIONARY){};
//                    driveDistance(-(MM_TO_IN(COUNTS_TO_MM(remaining))),PLAID);
//
////                    sprintf(message, "%f %f %f\r\n", remaining,COUNTS_TO_MM(remaining),MM_TO_IN(COUNTS_TO_MM(remaining)));
////                    NU32_WriteUART1(message);
//                } else if (collisionBottomRight == 1) {
//                    remaining = terminalCounts1 - position1;
//                    terminalCounts1 = 0;
//                    turnAngle(30);
//                    while(drivingState != STATIONARY){};
//                    driveDistance(-(MM_TO_IN(COUNTS_TO_MM(remaining))),PLAID);
//                }
//            }
//        }

        if (!NU32USER) {
            blah = time;
            while (time < blah + 1000){};
            firstSweep();
            secondSweep();
            exitAndResetOnRightAllWay();
            while (drivingState != STATIONARY){};
        }
}
    return 0;
}

//////ISRs
// Core Timer ISR
void __ISR(_CORE_TIMER_VECTOR, IPL7SRS) CoreTimerISR(void)
{
    // increment time by one every millisecond
    time++;

    // toggle led2 every second
    if (time%1000 == 0)
        NU32LED2 = !NU32LED2;

    WriteCoreTimer(0);              // set core timer counter to 0
    _CP0_SET_COMPARE(CORE_TICKS);   // must set CP0_COMPARE again after interrupt
    INTClearFlag(_CORE_TIMER_IRQ);  // clear the interrupt flag
}

// Timer4 ISR - for reading encoder at 250Hz
void __ISR(_TIMER_4_VECTOR, ipl5) Timer4ISR(void)
{
    // initalize all static variables
    static long oldPos1 = 0;
    static long oldPos2 = 0;
    static float vel1 = 0;
    static float vel2 = 0;
    static float e1 = 0;
    static float e2 = 0;
    static float e1Old = 0;
    static float e2Old = 0;
    static float e_int1 = 0;
    static float e_int2 = 0;
    static float e_dif1 = 0;
    static float e_dif2 = 0;
    static float e_tie = 0;
    static int update1 = 0;
    static int update2 = 0;

    static long overshootCounts = 0;
    static float stoppedDegrees = 0;
    static float overshootDegrees = 0;

    static long waitTime = 0;

    static float Kpadj = 0;
    static float Kdadj = 0;
    static float Kiadj = 0;
    
    int reset = R_NONE;

//    position1 = getEncoder1(FALSE);
//    position2 = getEncoder2(FALSE);
//    static int count = 0;
//    if (count == 50) {
//            sprintf(LCD_Out_Buffer, "%3.4f", POSITION_TO_ANGLE(position1, -position2));
//            LCDWriteString(LCD_Out_Buffer, 2, 1);
//            count = 0;
//        }
//    count++;

    // if motors are on
    if (drivingState != STATIONARY) {
        // make all encoder readings positive
        if (drivingState == FORWARD || drivingState == RESET_ANGLE_WALL) {
            Kpadj = 2;
            Kt = 1;
            position1 = getEncoder1(FALSE);
            position2 = getEncoder2(FALSE);
        } else if (drivingState == BACKWARD || drivingState == RESET_ANGLE_ZONE) {
            Kp = 28;
            Kd = 115;
            Kpadj = 4;
            Kdadj = 7;
            Kt = 1;
            position1 = -getEncoder1(FALSE);
            position2 = -1.00*getEncoder2(FALSE);
        } else if (drivingState == CCW) {
            Kpadj = 3;
            Kdadj = 7;
            Kp = 45;
            Kd = 180;
            Ki = 8;
            Kt = 5;
            position1 = -getEncoder1(FALSE);
            position2 = getEncoder2(FALSE);
        } else if (drivingState == CW){
            Kpadj = 3;
            Kp = 45;
            Kd = 180;
            Ki = 8;
            Kt = 5;
            position1 = getEncoder1(FALSE);
            position2 = -1.00*getEncoder2(FALSE);
        } else if (drivingState == COLOR_SWITCH) {
            if (lastColor == startingColor) {
                Kpadj = 2;
                Kdadj = 1;
                position1 = getEncoder1(FALSE);
                position2 = getEncoder2(FALSE);
            } else {
                Kp = 28;
                Kd = 115;
                Kpadj = 4;
                Kdadj = 7;
                Kt = 1;
                position1 = -getEncoder1(FALSE);
                position2 = -1.00*getEncoder2(FALSE);
            }
        }

        if (drivingMode == STATIONARY) {
            cps = 0;
        } else if (drivingMode == FAST) {
            cps = CPS_FAST;
        } else if (drivingMode == MEDIUM) {
            cps = CPS_MEDIUM;
        } else if (drivingMode == SLOW) {
            cps = CPS_SLOW;
        } else if (drivingMode == CORRECTER) {
            cps = CPS_CORRECTER;
        } else if (drivingMode == PLAID) {
            cps = CPS_PLAID;
        }

        // calculate current velocity of each wheel
        vel1 = (position1 - oldPos1);
        vel2 = (position2 - oldPos2);
        oldPos1 = position1;
        oldPos2 = position2;

        // the tie term keeps track of the difference between the motors
        e_tie = vel1 - vel2;


        // the proportional error term
        e1 += (cps/TMR4_FREQ) - vel1;
        e2 += (cps/TMR4_FREQ) - vel2;

        // the differentual error term
        e_dif1 = e1 - e1Old;
        e_dif2 = e2 - e2Old;
        e1Old = e1;
        e2Old = e2;

        // the integral term keeps track of the buildup of error
        e_int1 += e1;
        e_int2 += e2;

        // do not exceed windup
        if (e_int1 > WINDUP)
            e_int1 = WINDUP;
        if (e_int1 < -WINDUP)
            e_int1 = -WINDUP;
        if (e_int2 > WINDUP)
            e_int2 = WINDUP;
        if (e_int2 < -WINDUP)
            e_int2 = -WINDUP;

        if (((e1-e2) > 300))
            e1 = e2 + 200;

        // calculate the PWM needed to maintain velocity
        update1 = (((Kp+Kpadj)*e1) + ((Kd+Kdadj)*e_dif1) - (Kt*e_tie) + ((Ki+Kiadj)*e_int1))/K0;      // left motor
        update2 = ((Kp*e2) + (Kd*e_dif2) + (Kt*e_tie) + (Ki*e_int2))/K0;      // right motor

        // do not exceed PWM bounds
        if (update1 > MAX_PWM)
            update1 = MAX_PWM;
        if (update1 < 0)
            update1 = 0;
        if (update2 > MAX_PWM)
            update2 = MAX_PWM;
        if (update2 < 0)
            update2 = 0;

//        //for printing data more slowly to UART
//        static int count = 0;
//        if (count == 25) {
//            char message[100];
//            //sprintf(message, "%ld %lld\r\n", position1, position2);
//            sprintf(message, "vel: %f %f up: %d %d err: %f %f\r\n", vel1, vel2, update1,update2,e1,e2);
//            NU32_WriteUART1(message);
////            sprintf(NU32_RS232OutBuffer,"%d %d\n", (int)(10*vel1), (int)(10*vel2));
////            WriteString(UART1, NU32_RS232OutBuffer);
//            count = 0;
//        }
//        count++;

        // stop the motors if the desired position is reached
        if (drivingMode == PLAID || drivingMode == FAST || drivingMode == MEDIUM) {
            if (drivingState == FORWARD || drivingState == BACKWARD) {
                if (position1 >= terminalCounts1)
                    reset = R_STOP;
            } else if (drivingState == CCW || drivingState == CW) {
                if (POSITION_TO_ANGLE(position1,position2) >= terminalDegrees - BOUNDARY_ANGLE)
                    reset = R_SLOW;
            } else if (drivingState == COLOR_SWITCH) {
                if (lastColor != currentColor1 && lastColor != currentColor2)
                    reset = R_STOP;
            } else if (drivingState == RESET_ANGLE_WALL) {
                if (collisionTopLeft == 1 && EN1 == 1) {
                    EN1 = 0;
                    Kt = 0;
                    waitTime = time;
                    drivingMode = PLAID;
                }
                if (collisionTopRight == 1 && EN2 == 1) {
                    EN2 = 0;
                    Kt = 0;
                    waitTime = time;
                    drivingMode = PLAID;
                }
                if (EN1 == 0 && EN2 == 0) {
                     reset = R_STOP;
                     EN1 = 1;
                     EN2 = 1;
                }
                if (time > waitTime + 750 && (EN1==0 || EN2==0))
                    reset = R_STOP;
            } else if (drivingState == RESET_ANGLE_ZONE) {
                if (collisionBottomLeft == 1 && EN1 == 1) {
                    EN1 = 0;
                    Kt = 0;
                    waitTime = time;
                    drivingMode = PLAID;
                }
                if (collisionBottomRight == 1 && EN2 == 1) {
                    EN2 = 0;
                    Kt = 0;
                    waitTime = time;
                    drivingMode = PLAID;
                }
                if (EN1 == 0 && EN2 == 0) {
                     reset = R_STOP;
                     EN1 = 1;
                     EN2 = 1;
                }
                if (time > waitTime + 750 && (EN1==0 || EN2==0))
                    reset = R_STOP;
            }
        } else if (drivingMode == SLOW) {
            if (drivingState == FORWARD || drivingState == BACKWARD) {
                if (position1 >= terminalCounts1)
                    reset = R_STOP;
            } else if (drivingState == CCW || drivingState == CW) {
                if (POSITION_TO_ANGLE(position1,position2) >= terminalDegrees) {
                    reset = R_CORRECTER;
                }  
            }       
        } else if (drivingMode == CORRECTER) {
            if (drivingState == FORWARD || drivingState == BACKWARD) {
                if (position1 >= overshootCounts)
                    reset = R_STOP;
            } else if (drivingState == CCW || drivingState == CW) {
                if (POSITION_TO_ANGLE(position1,position2) >= overshootDegrees)
                    reset = R_STOP;
            }
        }
    }

    if (reset == R_STOP) {
        drivingState = STATIONARY;
        drivingMode = STATIONARY;
        Kp = 30;
        Kd = 120;
        Ki = 5;
        Kt = 10;
        Kpadj = 0;
        Kdadj = 0;
        Kiadj = 0;
        terminalCounts1 = 0;
        terminalDegrees = 0;
        oldPos1 = 0;
        oldPos2 = 0;
        vel1 = 0;
        vel2 = 0;
        e1 = 0;
        e2 = 0;
        e1Old = 0;
        e2Old = 0;
        e_int1 = 0;
        e_int2 = 0;
        e_dif1 = 0;
        e_dif2 = 0;
        e_tie = 0;
        update1 = 0;
        update2 = 0;
        stoppedDegrees = 0;
        overshootCounts = 0;
        overshootDegrees = 0;
        reset = R_NONE;
    } else if (reset == R_SLOW) {
        drivingMode = SLOW;
        reset = R_NONE;
    } else if (reset == R_CORRECTER) {
        // set cps to 0
        drivingMode = STATIONARY;

        // Stop the motors
        setMotorSpeed(0, 0);

        stoppedDegrees = POSITION_TO_ANGLE(position1,position2);

        // determine the inertial overshoot
        waitTime = time;
        while (time < waitTime + 100 + min(terminalDegrees,100)){};   // wait 1/10 second
        getEncoder1(FALSE);
        getEncoder2(FALSE);
        if (drivingState == FORWARD) {
            position1 = getEncoder1(FALSE);
            position2 = getEncoder2(FALSE);
        } else if (drivingState == BACKWARD) {
            position1 = -getEncoder1(FALSE);
            position2 = -getEncoder2(FALSE);
        } else if (drivingState == CCW) {
            position1 = -getEncoder1(FALSE);
            position2 = getEncoder2(FALSE);
        } else if (drivingState == CW) {
            position1 = getEncoder1(FALSE);
            position2 = -getEncoder2(FALSE);
        }
        overshootCounts = position1 - terminalCounts1;
        overshootDegrees = (POSITION_TO_ANGLE(position1, position2) - stoppedDegrees)/min(max((terminalDegrees/93+1.325),1.65),2.3);

        // change direction
        if (drivingState == FORWARD)
            drivingState = BACKWARD;
        else if (drivingState == BACKWARD)
            drivingState = FORWARD;
        else if (drivingState == CW)
            drivingState = CCW;
        else if (drivingState == CCW)
            drivingState = CW;
        DIR1 = !DIR1;
        DIR2 = !DIR2;

        // reset everything
        getEncoder1(TRUE);getEncoder2(TRUE);
        getEncoder1(TRUE);getEncoder2(TRUE);
        oldPos1 = 0;
        oldPos2 = 0;
        vel1 = 0;
        vel2 = 0;
        e1 = 0;
        e2 = 0;
        e1Old = 0;
        e2Old = 0;
        e_int1 = 0;
        e_int2 = 0;
        e_dif1 = 0;
        e_dif2 = 0;
        e_tie = 0;
        update1 = 0;
        update2 = 0;
        terminalCounts1 = 0;
        terminalDegrees = 0;

        // set driving mode to inertial correcter
        drivingMode = CORRECTER;
    } 

    setMotorSpeed(update1, update2);

    // clear interrupt flag and exit
    mT4ClearIntFlag();
} // end T4 Interrupt

// Timer5 ISR - for reading phototransisors at 10 Hz
void __ISR(_TIMER_5_VECTOR, ipl4) Timer5ISR(void)
{
    int i, j;
    //static int count = 0;
    //count++;
    int ptON[7], ptOFF[7], ptDIF[7];
    int collision[4];
    int crates = 0;
    long lastTime;
    static int firstTime = 0;
    int tempColor1 = 0;
    int tempColor2 = 0;
    static int previousColor1 = 0;
    static int previousColor2 = 0;
    
    LEDS = 1;
    lastTime = time;
    while (time<lastTime+2){}; // wait 2 ms
    for (i=COLOR_SENSOR_LEFT, j=0; i<=BB_TOWER_TOP; i++,j++)
        ptON[j] = ReadADC10(i);

    LEDS = 0;
    lastTime = time;
    while (time<lastTime+2){}; // wait 2 ms
    for (i=COLOR_SENSOR_LEFT, j=0; i<=BB_TOWER_TOP; i++,j++)
        ptOFF[j] = ReadADC10(i);

    for (j=0; j<7; j++)
        ptDIF[j] = ptON[j]-ptOFF[j];

    //if ((drivingState != STATIONARY
    // Color sensor 1
    if (ptDIF[0] < CS1_BP_THRESHOLD)
        tempColor1 = BLACK;
    else if (ptDIF[0] < CS1_PW_THRESHOLD )
        tempColor1 = PURPLE;
    else
        tempColor1 = WHITE;

    // Color sensor 2
    if (ptDIF[1] < CS2_BP_THRESHOLD)
        tempColor2 = BLACK;
    else if (ptDIF[1] < CS2_PW_THRESHOLD)
        tempColor2 = PURPLE;
    else
        tempColor2 = WHITE;

    if (firstTime == 0) {
        previousColor1 = tempColor1;
        previousColor2 = tempColor2;
    }

    // Color sensor 1
    if (tempColor1 == previousColor1) {
        if (tempColor1 == BLACK)
            currentColor1 = BLACK;
        else if (tempColor1 == PURPLE)
            currentColor1 = PURPLE;
        else
            currentColor1 = WHITE;
    }

    // Color sensor 2
    if (tempColor2 == previousColor2) {
        if (tempColor2 == BLACK)
            currentColor2 = BLACK;
        else if (tempColor2 == PURPLE)
            currentColor2 = PURPLE;
        else
            currentColor2 = WHITE;
    }

    previousColor1 = tempColor1;
    previousColor2 = tempColor2;

    // If first time, set starting color
    if (firstTime == 0) {
        if (currentColor1 == currentColor2 && currentColor1 != BLACK) {
            startingColor = currentColor1;
            firstTime++;    // never run this loop again
        }
    }

    if (currentColor1 != BLACK && currentColor2 != BLACK) {
        if (currentColor1 == currentColor2)
            currentColor = currentColor1;
        else
            currentColor = BOTH;
    }

    // breakbeam - chassis - front
    if (ptDIF[2] < BB_THRESHOLD)
        crateInFront = 1;
    else
        crateInFront = 0;

    // breakbeam - chassis - middle
    if (ptDIF[3] < BB_THRESHOLD)
        crateInMiddle = 1;
    else
        crateInMiddle = 0;

    // breakbeam - chassis - middle
    if (ptDIF[4] < BB_THRESHOLD)
        crates++;
    if (ptDIF[5] < BB_THRESHOLD)
        crates++;
    if (ptDIF[6] < BB_THRESHOLD)
        crates++;
    numCrates = crates;

    // collision detection
    for (i=COLLISION_TOP_LEFT, j=0; i<=COLLISION_BOTTOM_RIGHT; i++,j++)
        collision[j] = ReadADC10(i);

    if (collision[0] < COLLISION_THRESHOLD)
        collisionTopLeft = 1;
    else
        collisionTopLeft = 0;

    if (collision[1] < COLLISION_THRESHOLD) 
        collisionTopRight = 1;
    else
        collisionTopRight = 0;
    
    if (collision[2] < COLLISION_THRESHOLD) 
        collisionBottomLeft = 1;
    else
        collisionBottomLeft = 0;
    
    if (collision[3] < COLLISION_THRESHOLD) 
        collisionBottomRight = 1;
    else
        collisionBottomRight = 0;

//    int laseron, laseroff, laser;
//    LASER_LIGHT = 1;
//    lastTime = time;
//    while (time<lastTime+3){}; // wait 2 ms
//    laseron = ReadADC10(LASER_PT);
//
//    LASER_LIGHT = 0;
//    lastTime = time;
//    while (time<lastTime+3){}; // wait 2 ms
//    laseroff = ReadADC10(LASER_PT);
//
//    char message[100];
//    sprintf(message, "%d\r\n", laseron-laseroff);
//    NU32_WriteUART1(message);

//    char message[100];
//    sprintf(message, "%d %d %d %d \r\n", collisionTopLeft, collisionTopRight, collisionBottomLeft, collisionBottomRight);
//    NU32_WriteUART1(message);

//    char message[100];
//    sprintf(message, "%d %d %d %d %d %d %d\r\n", ptDIF[0], ptDIF[1], ptDIF[2], ptDIF[3], ptDIF[4], ptDIF[5], ptDIF[6]);
//    NU32_WriteUART1(message);

//    char message[100];
//    sprintf(message, "%d %d %d %d %d %d\r\n", startingColor, currentColor, currentColor1, currentColor2, ptDIF[0], ptDIF[1]);
//    NU32_WriteUART1(message);

    // clear interrupt flag and exit
    mT5ClearIntFlag();
} // end T5 Interrupt

void __ISR(_UART_1_VECTOR, ipl2) IntUart1Handler(void)
{
    // Is this an RX interrupt?
    if(INTGetFlag(INT_SOURCE_UART_RX(UART1)))
    {
        char data = UARTGetDataByte(UART1);
        PutCharacter(UART1,data);
        NU32LED1 = !NU32LED1;

        if (data == 'h')
            rotateFanArm(FAN_ARM_HORIZONTAL);
        if (data == 'v')
            rotateFanArm(FAN_ARM_VERTICAL);
        if (data == 'c')
            rotateTowerDoor(TOWER_DOOR_CLOSED);
        if (data == 'o')
            rotateTowerDoor(TOWER_DOOR_OPEN);
        if (data == 'a')
            rotateTowerDoor(TOWER_DOOR_AJAR);
        if (data == 'l')
            SetDCOC5PWM(LASER_LEFT);
        if (data == 'r')
            SetDCOC5PWM(LASER_RIGHT);
        if (data == 'k')
            SetDCOC5PWM(LASER_CENTER);
        if (data == 'f')
            FAN1 = !FAN1;
        if (data == 'g')
            FAN2 = !FAN2;
        if (data == 's')
            sweepLaser(3);
        if (data == 't')
            turnAngle(90);
        if (data == 'y')
            turnAngle(-90);
        if (data == 'u')
            resetAngle();

        // Clear the RX interrupt Flag
        INTClearFlag(INT_SOURCE_UART_RX(UART1));
    }

    // We don't care about TX interrupt
    if(INTGetFlag(INT_SOURCE_UART_TX(UART1))) {
        INTClearFlag(INT_SOURCE_UART_TX(UART1));
    }
}

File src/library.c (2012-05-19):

#include <plib.h>
#include "data.h"
#include "library.h"
#include "NU32.h"
#include "LCD.h"
#include "math.h"

// initalize the core timer
void initCoreTimer(void)
{
    _CP0_SET_COMPARE(CORE_TICKS);                      // CP0_COMPARE register set to 40 M
    mConfigIntCoreTimer(CT_INT_ON | CT_INT_PRIOR_7);   // enable CT interrupts with IPL7
    WriteCoreTimer(0);                                 // set core timer counter to 0
}

// set a 250Hz timer interrupt
void initTimer4Interrupt(void)
{
    OpenTimer4(T4_ON | T4_PS_1_256, TMR4_PR); // 80000000Hz / 256ps / 250Hz = 1250
    mT4SetIntPriority(5); // set Timer4 Interrupt Priority
    mT4ClearIntFlag(); // clear interrupt flag
    mT4IntEnable(1); // enable timer4 interrupts
}

// set a 10Hz timer interrupt
void initTimer5Interrupt(void)
{
    OpenTimer5(T5_ON | T5_PS_1_256, TMR5_PR); // 80000000Hz / 256ps / 10Hz = 31250
    mT5SetIntPriority(4); // set Timer5 Interrupt Priority
    mT5ClearIntFlag(); // clear interrupt flag
    mT5IntEnable(1); // enable timer5 interrupts
}

// initalize the digital inputs with pullup resistors, and turn change notifcation ISR on
void initChangeNotification(void)
{
    //mPORTBSetPinsDigitalIn(BIT_0| BIT_1 | BIT_2 | BIT_3); // Make B0, B1, B2, B3 digital inputs
    mCNOpen(CN_ON, CN2_ENABLE | CN3_ENABLE | CN4_ENABLE | CN5_ENABLE, CN2_PULLUP_ENABLE | CN3_PULLUP_ENABLE | CN4_PULLUP_ENABLE | CN5_PULLUP_ENABLE);

//    PORTB;  // Clear any mismatches that may already be there by reading the correct ports
//
//    mCNSetIntPriority(3);    // set change notifcation priority
//    mCNSetIntSubPriority(2); // set change notification subpriority
//    mCNClearIntFlag();
//    mCNIntEnable(1);        // enable change notifcation interrupts
}

// initalize the digital output pins 
// Note: motor enable and direction pins initalized in initOutputCompare();
//       encoder slave select pins initalized in initEncoderSPI();
void initDigitalOut(void)
{
    mPORTDSetPinsDigitalOut(BIT_10 | BIT_11 | BIT_12 | BIT_13);  // make D10, D11, D12, D13 digital outs
    LASER_LIGHT = 0;     // pin D10 - intially 0
    LEDS = 0;            // pin D11 - initially 0
    FAN1 = 0;            // pin D12 - initially 0
    FAN2 = 0;            // pin D13 - initially 0
}

// initialize the analog input
void initAnalogInput(void)
{
    // configure and enable the ADC
    CloseADC10();	// ensure the ADC is off before setting the configuration

    // define setup parameters for OpenADC10
    // Turn module on | output in integer | trigger mode auto | enable  autosample
    #define PARAM1  ADC_MODULE_ON | ADC_FORMAT_INTG | ADC_CLK_AUTO | ADC_AUTO_SAMPLING_ON

    // define setup parameters for OpenADC10
    // ADC ref external | disable offset test | enable scan mode | perform 8 samples | use one buffer | use MUXA mode
    #define PARAM2  ADC_VREF_AVDD_AVSS | ADC_OFFSET_CAL_DISABLE | ADC_SCAN_ON | ADC_SAMPLES_PER_INT_12 | ADC_ALT_BUF_OFF | ADC_ALT_INPUT_OFF
    // ** If you want to read more than 1 pin, change the 1 in ADC_SAMPLES_PER_INT_1 to the total number of pins you want

    // define setup parameters for OpenADC10
    // use ADC internal clock | set sample time
    #define PARAM3  ADC_CONV_CLK_INTERNAL_RC | ADC_SAMPLE_TIME_15

    // define setup parameters for OpenADC10
    #define PARAM4	ENABLE_AN0_ANA | ENABLE_AN1_ANA| ENABLE_AN2_ANA | ENABLE_AN3_ANA | ENABLE_AN6_ANA | ENABLE_AN7_ANA | ENABLE_AN8_ANA | ENABLE_AN9_ANA | ENABLE_AN10_ANA | ENABLE_AN11_ANA | ENABLE_AN12_ANA | ENABLE_AN13_ANA
    // ** If you want to read more pins, | (or) them together, like:
    // ** ENABLE_AN3_ANA | ENABLE_AN5_ANA | ENABLE_AN6_ANA
    // ** to read B3, B5 and B6

    // define setup parameters for OpenADC10
    // assign channels you don't want to scan
    #define PARAM5	SKIP_SCAN_AN4 | SKIP_SCAN_AN5 | SKIP_SCAN_AN14 | SKIP_SCAN_AN15
    // ** This one has all the pins that are not in PARAM4

    // use ground as neg ref for mux A, don't worry about it
    SetChanADC10( ADC_CH0_NEG_SAMPLEA_NVREF);
    OpenADC10( PARAM1, PARAM2, PARAM3, PARAM4, PARAM5 ); // configure ADC using parameters define above

    EnableADC10(); // Enable the ADC
}

// Initalize the 5 PWM pins + relevant digital outs
void initOutputCompare(void)
{
    LATD  |= 0x0000; // set all of the outputs on D to low
    TRISD &= 0xFE1F; // set pins 5, 6, 7, 8 in D to outputs (0xFF95 = 0b1111111000011111)

    // use Timer2 for a 1kHz PWM signal for the motors on the h-bridge
    OpenTimer2(T2_ON | T2_PS_1_64, 1250); // 80000000Hz / 64ps / 1000Hz = 1250

    // Left Motor - pin D0
    OpenOC1(OC_ON | OC_TIMER2_SRC | OC_PWM_FAULT_PIN_DISABLE, 0, 0);
    SetDCOC1PWM(0); // duty cycle from 0-1250

    // Right Motor - pin D1
    OpenOC2(OC_ON | OC_TIMER2_SRC | OC_PWM_FAULT_PIN_DISABLE, 0, 0);
    SetDCOC2PWM(0); // duty cycle from 0-1250

    // use Timer3 for a 50Hz PWM signal for the RC servo motor
    OpenTimer3(T3_ON | T2_PS_1_64, 25000); // 80000000Hz / 64ps / 50Hz = 25000

    // Fan Arm - pin D2
    OpenOC3(OC_ON | OC_TIMER3_SRC | OC_PWM_FAULT_PIN_DISABLE, 0, 0);
    SetDCOC3PWM(FAN_ARM_VERTICAL); // duty cycle from 0-25000

    // Tower Door - pin D3
    OpenOC4(OC_ON | OC_TIMER3_SRC | OC_PWM_FAULT_PIN_DISABLE, 0, 0);
    SetDCOC4PWM(TOWER_DOOR_CLOSED); // duty cycle from 0-25000

    // Laser - pin D4
    OpenOC5(OC_ON | OC_TIMER3_SRC | OC_PWM_FAULT_PIN_DISABLE, 0, 0);
    SetDCOC5PWM(LASER_LEFT); // duty cycle from 0-25000

    // Turn Motors ON
    EN1 = 1;
    EN2 = 1;

    // Drive Forward
    DIR1 = 0;
    DIR2 = 0;

    // initalize speed
    setMotorSpeed(0,0);
}

// initialize SPI communication with the dsPIC at 8MHz + relvant digital outs
// Uses SPI4, pins are: SDI4:F4-RP14, SDO4:F5-RP13, SCK4:F13-RP12
void initEncoderSPI(void) {
    TRISFbits.TRISF12 = 0;      // pin F12 - digital out
    TRISFbits.TRISF3 = 0;       // pin F3 - digital out
    SLAVE_SELECT1 = 1;
    SLAVE_SELECT2 = 1;

    int data = 0;
    SPI4CON = 0; // stop and reset SPI4
    data = SPI4BUF; // clear the rx buffer
    SPI4BRG = 0x4; // bit rate to 8MHz, SPI4BRG = 80000000/(2*desired)-1
    SPI4STATCLR = 0x40; // clear overflow
    SPI4CON = 0x8620; // SPI ON, 16 bit xfer, SMP=1, MSTR
}
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

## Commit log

2012-01-27 Milestone 1
    - If a pushbutton is pressed, read the value of a potentiometer and change the brightness of an LED to the corresponding value with PWM
2012-02-24 Milestone 2
    - Optically isolate a motor
    - Read a potentiometer and write its voltage to the LCD
    - Control the motor velocity based on the potentiometer reading
    - Control an RC servo
    - Detect a 3/4" wide black line on white paper with a phototransistor and LED
2012-04-11 Chassis Milestone
    - Demonstrate a robot chassis that can drive around the arena, bonus points for following a line, detecting and moving towards the moving goals, and detecting and moving towards a crate
2012-06-05 Add model files
    [breakoutboard.SLDPRT, caster.SLDASM, caster_bridge.DXF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]
